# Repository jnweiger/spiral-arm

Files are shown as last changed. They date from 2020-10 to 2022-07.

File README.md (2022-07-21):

# Spiral Arm
An articulated arm made out of plywood. Its movement reminds me of an unfolding fern leaf, or a (somewhat stiff) octopus arm.

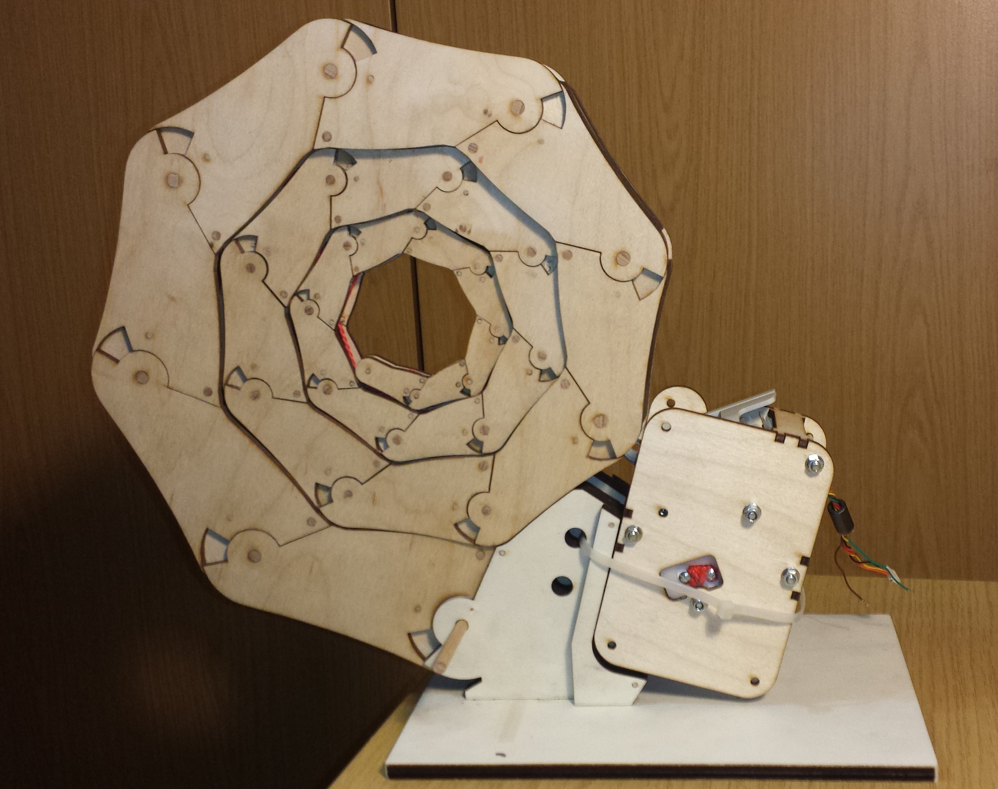
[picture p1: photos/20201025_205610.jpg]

  
This object was [inspired by John Edmark](http://www.johnedmark.com/spirals1/2016/4/29/roll-up-spiral),
who also invented the famous [helicone](http://www.johnedmark.com/rotating1/2016/4/29/helicone-an-interactive-kinetic-sculpture).

The lasercut parts are designed with inkscape. The sides of the arm are drawn in their rolled up position, they almost completely fill the plane.
You can still see how the grains of wood continue, when the arm fully rolled up.
I am adding different amounts of spacers between the two sides, to that the arm becomes a more natural 3-dimensional object.
The sides are cut out of 4mm birch plywood using arm-8er-shaped_laser3mm.svg (arm-8er-shaped_laser4mm.svg has the same for 3mm sides).
Either svg file also includes the needed spacers. For the spacers you need 3, 4 and 5 mm plywood, so that they can be stacked for all the 
different widths needed. See spacers.txt for the exact stacking. The shafts for mounting the segments are cut from beechwood rods with are 
6mm, 4mm, 3mm, and 2mm diameter. The 2mm ones are simply toothpics. I love toothpicks. You'll need lots of them, the often also serve as alignment pins.
My design includes 26 segments, with 8 segments per revolution.

You can hold the arm in your hands and pull the string to play with it. But as it is rather large and heavy, I also made a mount and an electric drive for it.

The mount is made out of 8mm plywood. Gluing the tabs firmly into the base plate is important. As the arm gives a strong pull there, when fully extended.
The base should be secured to the table with a clamp or several kg of counterweight to prevent it from flipping over. 
There are several holes in the base. You can use them to mount the base on a tripod (if you dare), or connect multiple bases side by side fanning out the arms in
in 15°, 30° or 45° angle (just in case you want to complete an octopus eventually).

The electric drive is based on an inexpensive worm gear motor found on ebay. It runs from 12v and takes less than 1A. 
It is built into a gearbox with lasercut gears from 3mm POM and a 3D-printed spool for winding up the string. The 3D-print design was made with FreeCAD.
All the STL-files in the drive folder were exported from the drum.FCstd drawing.

The motor is controlled by an Atmel ATTINY 2313 microcontroller connected to an L298N motor bridge. 
the logic is very simple. The winds up the string, until the arm is fully curled up and hits a push-button in the mount. Then the motor rotation is reversed, so that it unrolls again. There is no reversal needed for the unrolled position, as the spool simply winds up the string again after it was fully unrolled. 

You can also use an arudino-nano or similar instead of the bare metal 2313 -- programming a nano or uno is easier than. But for some reason I prefered to be minimalistic with the electronics. (Well, the 128 bytes RAM are almost full.)

If you can come up with a mechanical reversal switch that reliably works with this arm, please let me know. I failed to come up with something sufficiently robust, and went for the electronic solution instead. 

## Publications

* [Thingiverse](https://www.thingiverse.com/thing:4860603)

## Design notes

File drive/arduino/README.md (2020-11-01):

Program a blink sketch into an attiny2313
=========================================

I have an 
* old 16pin DIL programming clip
* an USBtiny ISP
* adruino IDE 1.8.13
* avrdude installed (for its /lib/udev/rules.d/60-avrdude.rules)

The Tiny2313 is a 20pin chip.
To program that one, we break lose one leg of the 16in clip and extend it by two pins.
This is the ground pin.

To verify program success, we solder an LED with a 330ohm resistor between GND and the next 
available pin on the clip, Pin 7.

In arduino IDE load the Examples -> 01.Basics -> Blink.
Instead of BUILTIN_LED use PIN_PD3. (Yes we can use Atmel Pin nam PD3, no need for consult a fancy arduino specific numbering pattern!)

Prefernces -> Additional Boardmanager URLs ->
 add to the list: http://drazzy.com/package_drazzy.com_index.json

Tools -> Board -> Board Manager
  -> locate ATTinyCore by Spence Konde -> install.

Tools -> Board: 2313 (no bootloader)
Tools -> Chip: 2313 (no bootloader)
Tools -> Clock: 1Mhz internal
Tools -> Port: /dev/ttyACM0
Tools -> Programmer: USBtinyISP SLOW		- the fast one does not work for me.

disconnect, reconnect the USBtinyISP dongle. The green led comes on.

Save, Upload, The red led on the USBtinyISP is on while uploading.

There will be a compiler warning:
  Global variables use 105 bytes (82%) of dynamic memory, leaving 23 bytes for local variables. Maximum is 128 bytes.
  Low memory available, stability problems may occur.
That is fine, we currently use 2 bytes of local variables. Need a 4313 if we run into trouble here. It has 256 bytes ram. tha tis twice as much!

When upload is done, the LED on the clip starts blinking.
SUCCESS!

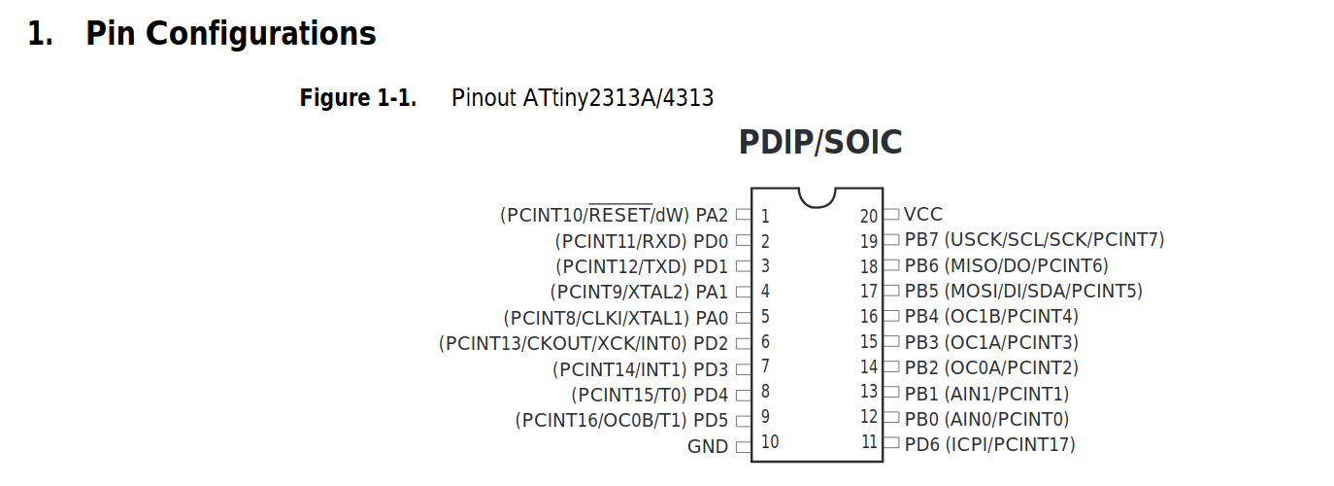
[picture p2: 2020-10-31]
drive/arduino/tn2313-pinout.png

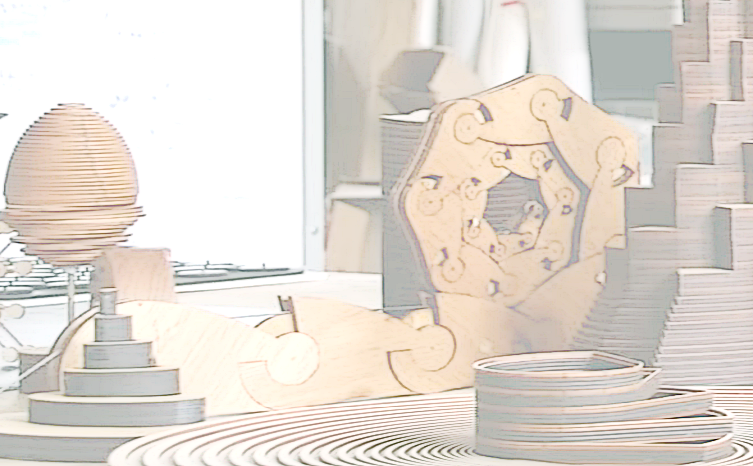
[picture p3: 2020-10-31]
photos/Screenshot from 2020-09-27 16-01-40.png

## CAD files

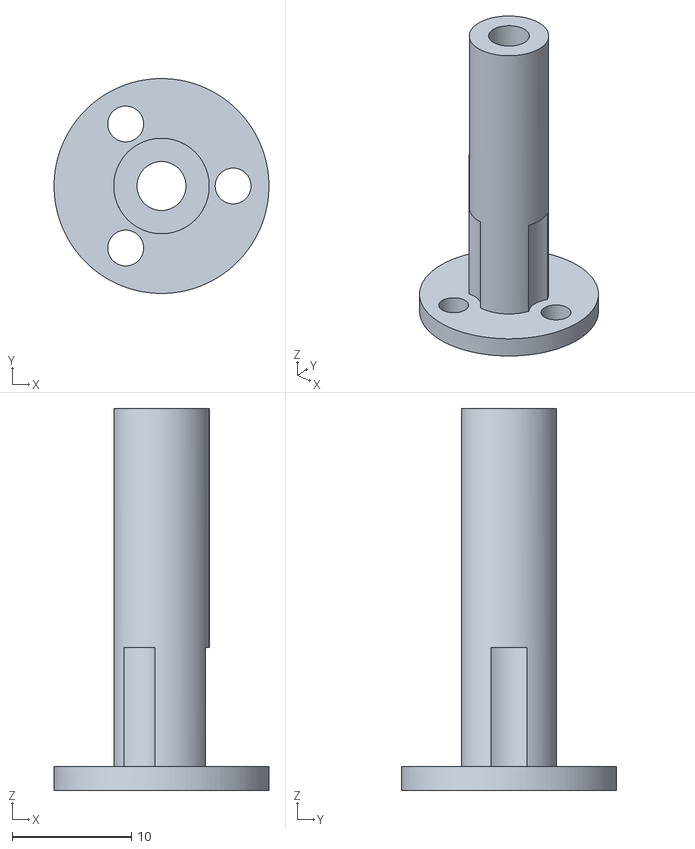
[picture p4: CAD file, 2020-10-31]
drive/shaft.stl
18.0 x 18.0 x 32.0

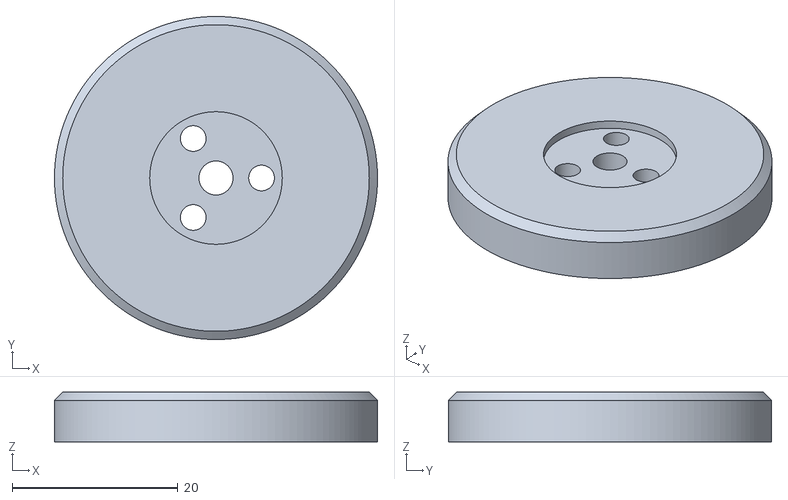
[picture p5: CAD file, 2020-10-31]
drive/drum_bot.stl
39.0 x 39.0 x 6.00

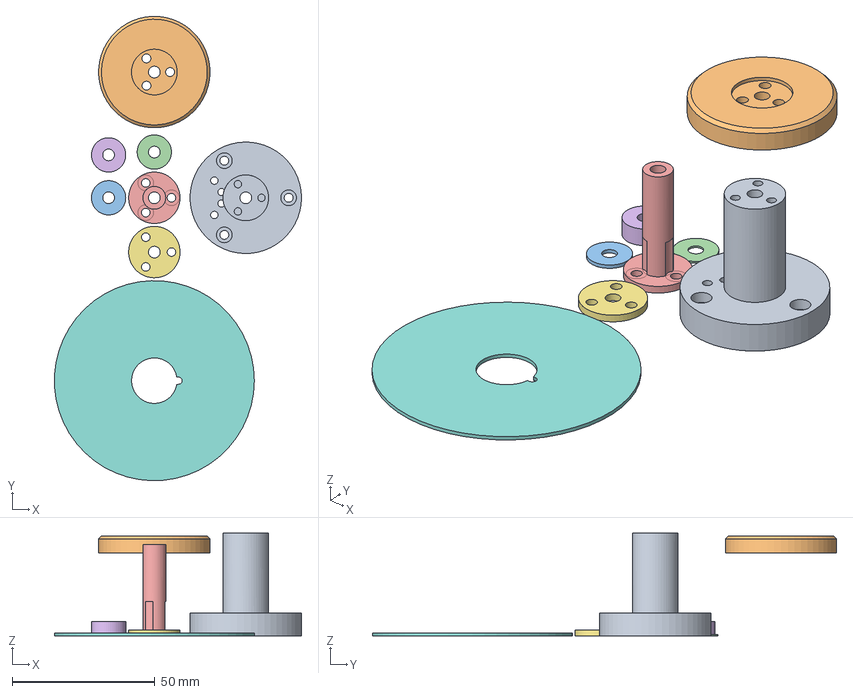
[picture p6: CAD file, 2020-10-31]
drive/drum.FCStd
86.4 x 162.5 x 36.0 mm
drum_top
drum_bot
washer_1mm
washer_0.5mm
shaft
washer_5mm
shaft_washer
safety_disc

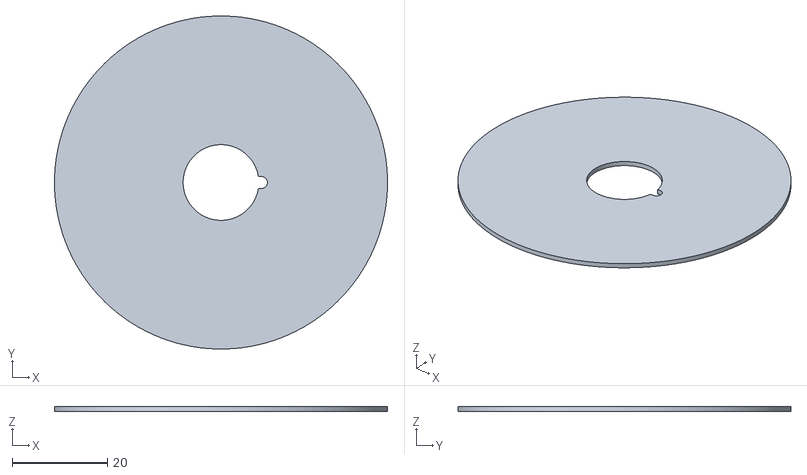
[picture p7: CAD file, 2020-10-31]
drive/safety_disc.stl
70.0 x 70.0 x 1.00

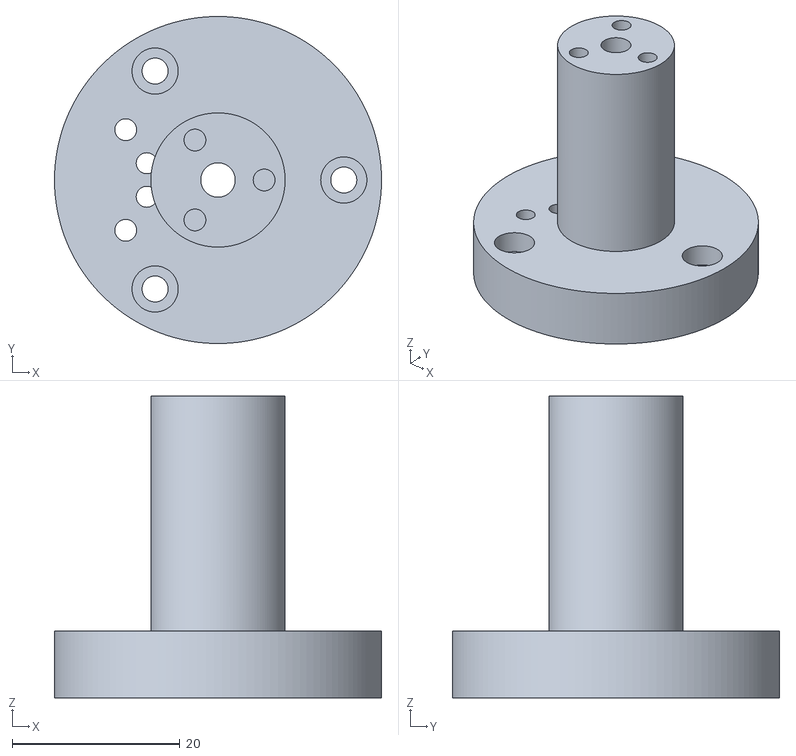
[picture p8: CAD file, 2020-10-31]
drive/drum_top.stl
39.0 x 39.0 x 36.0

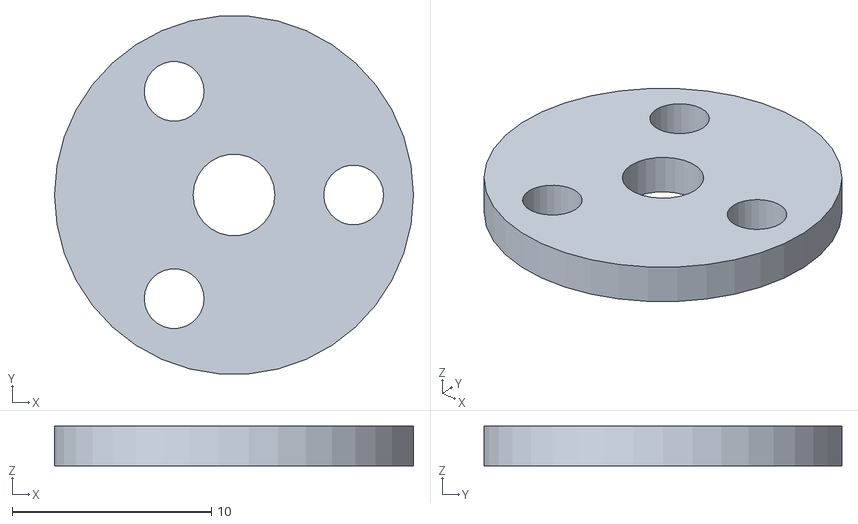
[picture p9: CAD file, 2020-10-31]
drive/shaft_washer.stl
18.0 x 17.9 x 2.00

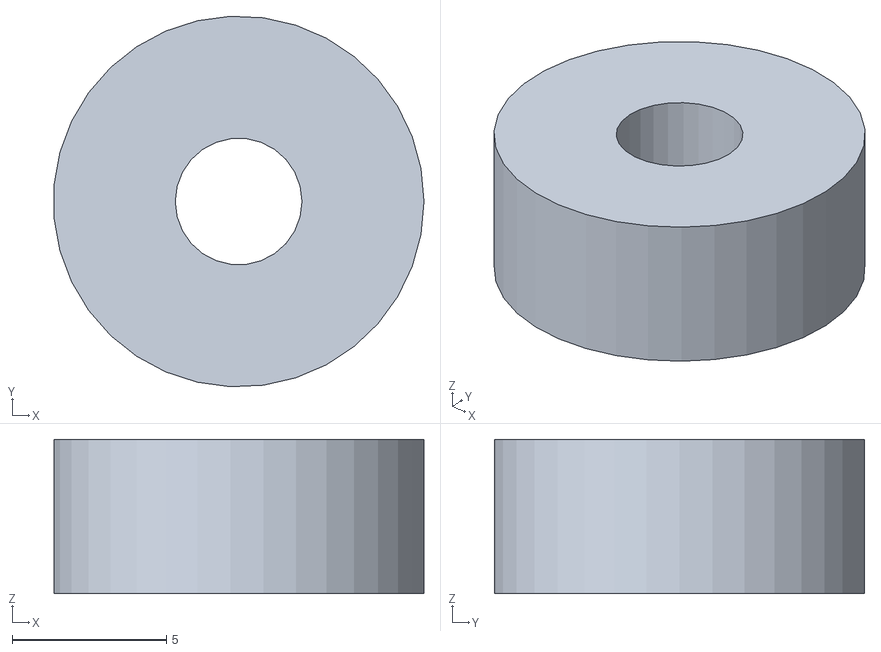
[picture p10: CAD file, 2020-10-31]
drive/washer_5mm.stl
12.0 x 12.0 x 5.00

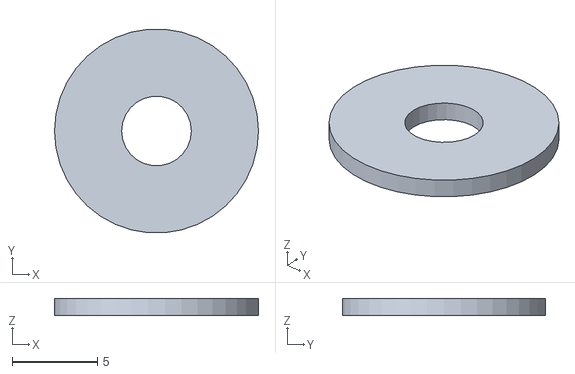
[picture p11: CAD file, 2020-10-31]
drive/washer_1mm.stl
12.0 x 12.0 x 1.00

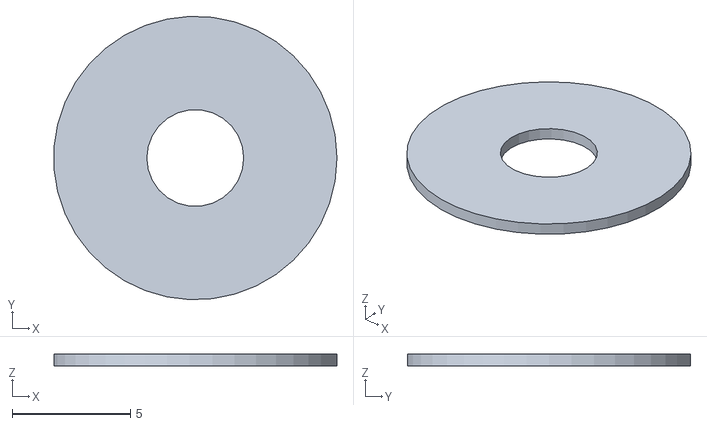
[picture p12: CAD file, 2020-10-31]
drive/washer_0.5mm.stl
12.0 x 12.0 x 0.5

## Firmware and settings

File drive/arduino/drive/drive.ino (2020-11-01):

/*
 * Motor reverse switch
 * Control one or two motors via L298N drivers.
 *
 * When switch 1 is pressed, motor 1 pauses PAUSE_TIME, then reverses its direction.
 * Same for switch 2 and motor 2.
 * The switches are disabled (ignored) during the pause and for SWITCH_DEBOUNCE_TIME afterwards for debouncing.
 * Optional function do_wink() can do some fun with the tip of the arm when extended.
 *
 * Switch 1: PIN_PB1   13
 * Switch 2: PIN_PB0   12
 *
 * Motor 1: PIN_PD2 + PIN_PD3   6,7
 * Motor 2: PIN_PD4 + PIN_PD5   8,9
 *
 * Flash LED: PIN_PB2   14
 *
 * v1.0 2020-10-29, jw	- simple working reversal switch.
 * v1.1 2020-10-31, jw	- timebase 10msec, introduced struct motor and do_motor() instead of many global vars and duplicated code.
 * v1.2 2020-10-31, jw	- pwm_pattern instroduced. slow start after button press, ACCEL_TIME=10 is just fine.
 * v1.3 2020-11-1, jw	- added midway fun with do_wink()
 */


uint16_t led_cnt = 0;
#define LED_INTERVALL 50		// unit of 10 msec

#define SWITCH_PRESSED LOW		/* Switch is connected to GND. Default: HIGH due to pullup */
#define SWITCH_DEBOUNCE_TIME 100	// unit of 10 msec
#define PAUSE_TIME 400			// unit of 10 msec. remain fully rolled up.
#define ACCEL_TIME 10			// unit of 80 msec. Softstart ramp.

#define WINK_START_OFFSET_TIME 600	// unit of 10 msec. Avoid hitting "exactly the unrolled point, where the string is loose"
#define WINK_SLOW_TIME 100		// unit of 10 msec. move slow before and after winking
#define WINK_SLOW_PWM 2			// which pwm_pattern to use for wink slow down.
#define WINK_MOVE_TIME 150		// unit of 10 msec. how long one wink move takes.


typedef struct {
  uint8_t switch_pin;		// Input pin for the reverse button. MUST INITIALIZE!
  uint8_t bridge1_pin;		// Output pin1 for the L298N bridge. MUST INITIALIZE!
  uint8_t bridge2_pin;		// Output pin2 for the L298N bridge. MUST INITIALIZE!

  uint8_t accel_cnt;		// Count down until next higher speed.
  uint8_t pwm_speed;		// Which pwm_pattern array we use. 0 = 25%, 6 = 100%
  uint8_t pwm_bit;		// Which pwm bit position we use.
  uint8_t fwd;			// Boolean
  uint16_t debounce_cnt;	// Count down while deboucing reversal switch
  uint16_t pause_cnt; 		// Count down while motor is pausing
  uint16_t loop_time_interval; 	// How many loops we had between the last two button presses
  uint16_t time_cnt; 		// Count up since the last button press.
} MOTOR;

MOTOR m1 = { PIN_PB1, PIN_PD2, PIN_PD3, ACCEL_TIME };
MOTOR m2 = { PIN_PB0, PIN_PD4, PIN_PD5, ACCEL_TIME };

#define N_PWM_PATTTERN 7
#define FULL_SPEED	(N_PWM_PATTTERN-1)
uint8_t pwm_pattern[N_PWM_PATTTERN][8] = 	// we only run at 100 Hz, so we better spread out the bits to achieve higher effective frequencies and less stutter.
{
  { 1,0,0,0,1,0,0,0 },  // 0:	2/8 = 25%
  { 1,0,0,1,0,1,0,0 },	// 1:	3/8 = 37%
  { 1,0,1,0,1,0,1,0 },  // 2:	4/8 = 50%
  { 1,1,0,1,0,1,1,0 },	// 3:	5/8 = 62%
  { 1,1,1,0,1,1,1,0 },	// 4:	6/8 = 75%
  { 1,1,1,1,1,1,1,0 },	// 5:	7/8 = 88%
  { 1,1,1,1,1,1,1,1 } 	// 6:	8/8 =100%
};


void do_wink(MOTOR *m)
{
  /*
   * This is a fun function.
   * We try to find the midpoint of the movement, when the arm is fully extended and starting to roll backwards.
   * Then we examine a random number (the last 3 bits of the loop_time_interval)
   * and based on that, we manipulate the motor, so that goes backward forward a few times.
   * The idea is that the little finger at the tip of the arm then does some inviting guesture.
   * In 5 out of 8 cases, we do nothing. Else we wink once, twice or 3 times.
   */
  uint16_t timer = m->time_cnt;
  if (m->loop_time_interval != 0 && timer > PAUSE_TIME+PAUSE_TIME+SWITCH_DEBOUNCE_TIME)	// do nothing, when we don't know the loop time, or when just starting a loop
    {
      uint16_t midpoint = WINK_START_OFFSET_TIME + (m->loop_time_interval) >> 1;
      uint8_t action    = m->loop_time_interval & 0x7;

      if (action < 3)
	{
	  if (		timer == midpoint - WINK_SLOW_TIME)
            {
								m->accel_cnt = 100;		// no auto-acceleration while we play here.
								m->pwm_speed = WINK_SLOW_PWM; 	// when at midpoint, we slow down.
	    }
	  if (		timer == midpoint + 0 * WINK_MOVE_TIME)	m->fwd = 1 - m->fwd;		// reverse motor
	  if (		timer == midpoint + 1 * WINK_MOVE_TIME)	m->fwd = 1 - m->fwd;		// a second later, we reverse again.
	  if (action < 2)		           						// do a second and maybe even a third wink?
	    {
	      if (	timer == midpoint + 2 * WINK_MOVE_TIME)	m->fwd = 1 - m->fwd;		// reverse again
	      if (	timer == midpoint + 3 * WINK_MOVE_TIME)	m->fwd = 1 - m->fwd;		// and again
	      if (action < 1)		           						// do a third wink?
		{
		  if (	timer == midpoint + 4 * WINK_MOVE_TIME)	m->fwd = 1 - m->fwd;		// reverse again
		  if (	timer == midpoint + 5 * WINK_MOVE_TIME)	m->fwd = 1 - m->fwd;		// and again
		}
              else if (	timer == midpoint + 2 * WINK_MOVE_TIME)	m->pwm_speed = FULL_SPEED; 	// normal speed after only one wink
	    }
          else if (	timer == midpoint + 4 * WINK_MOVE_TIME)	m->pwm_speed = FULL_SPEED; 	// normal speed after two winks
          if (		timer == midpoint + 6 * WINK_MOVE_TIME)	m->pwm_speed = FULL_SPEED; 	// normal speed in any case.
	}
    }
}


void do_motor(MOTOR *m)
{
  if (m->debounce_cnt == 0)
  {
    if (digitalRead(m->switch_pin) == SWITCH_PRESSED)
    {
      m->fwd = 1 - m->fwd;  /* reverse that motor */
      m->debounce_cnt = SWITCH_DEBOUNCE_TIME;
      m->pause_cnt = PAUSE_TIME;
      m->pwm_speed = 0;			// prepare slow start after button press
      m->accel_cnt = ACCEL_TIME;	// prepare slow start after button press

      m->loop_time_interval = m->time_cnt;	// store frome the last round.
      m->time_cnt = 0;
    }
  }
  else
  {
    if (m->pause_cnt > 0)
      m->pause_cnt--;
    else
      m->debounce_cnt--;
  }
  m->time_cnt++;

  uint8_t pulse = 0;
  if (m->pause_cnt == 0)
    {
      // advance pwm pattern and acceleration only when unpaused
      uint8_t bit = m->pwm_bit;
      pulse = pwm_pattern[m->pwm_speed][bit];
      if (++bit >= sizeof(pwm_pattern[0]))
        {
	  bit = 0;
          if (m->accel_cnt > 0)		// remain a bit longer at this speed?
            {
              m->accel_cnt--;
            }
          else if (m->pwm_speed < N_PWM_PATTTERN-1)	// can we switch to the next higher speed?
            {
	      m->pwm_speed++;
              m->accel_cnt = ACCEL_TIME;	// maintain that new speed for another acceleraton timer round.
            }
	  // if we are already at highest speed, we let accel_cnt drop to zero and it remains there.
        }
      m->pwm_bit = bit;	// regardless of speed and acceleration, the pwm_bit loops from 0 to 7 and back to 0.
    }

  if (pulse)
  {
    if (m->fwd)
    {
      digitalWrite(m->bridge1_pin, HIGH);
      digitalWrite(m->bridge2_pin, LOW);
    }
    else
    {
      digitalWrite(m->bridge1_pin, LOW);
      digitalWrite(m->bridge2_pin, HIGH);
    }
  }
  else // pwm pulse is low, or motor is paused.
  {
    digitalWrite(m->bridge1_pin, LOW);
    digitalWrite(m->bridge2_pin, LOW);
  }
}


void setup() {
  pinMode(PIN_PD2, OUTPUT);
  pinMode(PIN_PD3, OUTPUT);
  pinMode(PIN_PD4, OUTPUT);
  pinMode(PIN_PD5, OUTPUT);

  pinMode(PIN_PB2, OUTPUT);

  pinMode(PIN_PB0, INPUT_PULLUP);
  pinMode(PIN_PB1, INPUT_PULLUP);
}

void loop() {

  do_motor(&m1);
  do_motor(&m2);

  do_wink(&m1);
  do_wink(&m2);

  led_cnt++;
  if (led_cnt > LED_INTERVALL)
    led_cnt = 0;
  if (led_cnt == 0)
    digitalWrite(PIN_PB2, HIGH);
  else
    digitalWrite(PIN_PB2, LOW);

  delay(10);                       // wait 10 msec
}

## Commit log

2020-10-31 initial checking of almost everything...
    [drum.FCStd, drum_bot.stl, drum_top.stl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]
2020-10-31 mount can now also do the promised 45° angle. The shape gets weirder as expected due to this :-)
2020-11-01 di ot a bit later...
2020-11-01 arm mount 1° up.
2022-07-24 cable box added.
